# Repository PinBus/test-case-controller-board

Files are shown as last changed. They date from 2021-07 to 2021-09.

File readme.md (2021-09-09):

# Test-case Controller Board - Rev. 1.0

This board has been developed to control demo setups. It is essentially a smaller sized pinball machine controller. This board is based on the Arduino Uno, paired with a PCA9685 breakout board, eight MOSFETs and a four by four input matrix.

You will need to have a stencil made to make this board yourself. The SMD part footprints are not made for hand soldering.

**Warning: These designs are made as part of a hobby project and thus come with no guarantees. Do not use these designs in for any critical systems! Working with voltages higher than +40V can be potentially dangerous, please take appropriate safety measures!**

## Optional parts

 - Connectors **J2** and **J3** are optional. These headers expose the I2C bus and UART respectively.
 - Connectors **J4**, **J5**, and **J6** are optional. These headers expose the microcontroller pins.
 - Connector **J7** or **J8** are optional. These connectors are connected to the +5V rail. You will need at least one to power the board. The other connector can be used to power another board.
 - Connector **J9** or **J10** are optional. These connectors are connected to the +48V rail. You will need at least one when using the MOSFETs. The other connector can be used to power another board.
 - MOSFETs **Q1** thru **Q8** are optional:
   - Do not populate **R4**, **R6**, connector **SOL0**, and **D3** when not using **Q1**;
   - Do not populate **R8**, **R10**, connector **SOL1**, and **D4** when not using **Q2**;
   - Do not populate **R5**, **R7**, connector **SOL2**, and **D5** when not using **Q3**;
   - Do not populate **R9**, **R11**, connector **SOL3**, and **D6** when not using **Q4**;
   - Do not populate **R12**, **R14**, connector **SOL4**, and **D7** when not using **Q5**;
   - Do not populate **R16**, **R18**, connector **SOL5**, and **D8** when not using **Q6**;
   - Do not populate **R13**, **R15**, connector **SOL6**, and **D9** when not using **Q7**;
   - Do not populate **R17**, **R19**, connector **SOL7**, and **D10** when not using **Q8**;
 - When not using a MOSFET, you can use its pin on the PCA9685 to drive an LED:
   - Populate **LED0** if **Q1** is not used;
   - Populate **LED1** if **Q2** is not used;
   - Populate **LED2** if **Q3** is not used;
   - Populate **LED3** if **Q4** is not used;
   - Populate **LED4** if **Q5** is not used;
   - Populate **LED5** if **Q6** is not used;
   - Populate **LED6** if **Q7** is not used;
   - Populate **LED7** if **Q8** is not used;
 - **SOL0** and **SOL2** can be populated with either a 2 pin or a 3 pin connector:
   - Do not populate **SOL1** when **SOL0** is populated with a 3 pin connector;
   - Do not populate **SOL3** when **SOL2** is populated with a 3 pin connector;
 - All connectors and diodes making up the input matrix are optional:
   - Bridge **JP3** thru **JP6** to enable columns;
   - Bridge **JP7** thru **JP10** to enable rows;
 - Capacitors **C6** thru **C9** are optional. Populating **C6** is recommended. Populate others if needed.
 - Capacitors **C10** thru **C13** are optional. Populate if needed.

## BOM

| Identifiers | Quantity | Part number | Manufacturer | Footprint | Description |
| --- | ---: | --- | --- | --- | --- |
| C1 | 1x | CL10A475KQ8NNWC | Samsung Electro-Mechanics | 0603 | Capacitor, MLCC, 4.7μF, 10V |
| C2, C3, C4, C5 | 4x | GRM188R60J476ME15J  | Murata Electronics | 0603 | Capacitor, MLCC, 47μF, 6.3V |
| C6, C7, C8, C9 | 4x | URS1A470MDD1TA | Nichicon | ⌀5mm / 2mm  | Capacitor, Electrolytic, 47μ, 10V |
| C10, C11, C12, C13 | 4x | UVZ1J101MPD | Nichicon | ⌀10mm / 5mm | Capacitor, Electrolytic, 100μF, 63V |
| C14 | 1x | LMK107BBJ106MALT | Taiyo Yuden | 0603 | Capacitor, MLCC, 10μF, 10V |
| D1 | 1x | 150060RS75000 | Wurth Elektronik | 0603 | LED, Red |
| D2 | 1x | 150060GS75000 | Wurth Elektronik | 0603 | LED, Green |
| D3, D4, D5, D6, D7, D8, D9, D10 | 8x | S1M-13-F | Diodes Incorporated | SMA | Diode, rectifier, 1A, 1000V |
| D11, D12, D13, D14, D15, D16, D17, D18, D19, D20, D21, D22, D23, D24, D25, D26 | 16x | 1N4148W-G3-08 | Vishay / Dale | SOD-123 | Diode, general purpose, 150mA, 100V |
| J1 | 1x | | | 2.54mm | Connector, 2x3, Pin header |
| J2, J3 | 2x | B4B-XH-A(LF)(SN) | JST | 2.50mm | Connector, 1x4 |
| J4, J5 | 2x | | | 2.54mm | Connector, 1x8, pin header |
| J6 | 1x | | | 2.54mm | Connector, 1x6, pin header |
| J7, J8, LED0, LED1, LED2, LED3, LED4, LED5, LED6, LED7, LED8, LED9, LED10, LED11, LED12, LED13, LED14, LED15, MTX-0x0, MTX-0x1, MTX-0x2, MTX-0x3, MTX-1x0, MTX-1x1, MTX-1x2, MTX-1x3, MTX-2x0, MTX-2x1, MTX-2x2, MTX-2x3, MTX-3x0, MTX-3x1, MTX-3x2, MTX-3x3 | 34x | B2B-XH-A(LF)(SN) | JST | 2.50mm | Connector, 1x2 |
| J9, J10, SOL0, SOL1, SOL2, SOL3, SOL4, SOL5, SOL6, SOL7 | 10x | B2P-VH _or_ 1-1123723-3 | JST _or_ TE Connectivity | 3.96mm | Connector, 1x2 |
| JP1, JP2 | 2x | | | 2.54mm | Jumper wire |
| SOL0, SOL2 | 2x | B3P-VH _or_ 1-1123723-2 | JST _or_ TE Connectivity | 3.96mm | Connector, 1x3 |
| Q1, Q2, Q3, Q4, Q5, Q6, Q7, Q8 | 8x | IRL540NPBF | Infineon / IR | TO-220 | MOSFET, 100V, 36A |
| R1 | 1x | CRCW06034K70JNEAC | Vishay / Dale | 0603 | Resistor, 4.7kΩ |
| R2, R3 | 2x | CRCW06031K00FKEAC | Vishay / Dale | 0603 | Resistor, 1kΩ |
| R4, R5, R8, R9, R12, R13, R16, R17 | 8x | CRCW060310R0FKEAC | Vishay / Dale | 0603 | Resistor, 10Ω |
| R6, R7, R10, R11, R14, R15, R18, R19, R20, R21, R22, R23, R24, R25, R26, R27, R28, R29, R30, R31, R32 | 21x | CRCW060310K0JNEAC | Vishay / Dale | 0603 | Resistor, 10kΩ |
| SW1 | 1x | PTS810SJM250SMTRLFS | C&K | - | Switch |
| U1 | 1x | ATmega328P-AU | Microchip Technology | TQFP-32 | Microcontroller |
| U2 | 1x | PCA9685PW,112 | NXP Semiconductors | TSSOP-28 | PWM driver |
| Y1 | 1x | CSTNE16M0V53L00ZR0  | Murata Electronics | - | Resonator, 16MHz, 15pF |

### Pin headers

You can use either the [JST VH series](https://www.jst-mfg.com/product/detail_e.php?series=262) pin headers or the TE Connectivity Economy Power series pin headers. These pin headers are known to fit, other 3.96mm pin pitch pin headers might also fit.

 - Order the JST SVH-21T-P1.1 crimp contacts (0.34mm² - 0.75mm²) for use with the JST pin headers
 - Order JST VHR-2N connector housing for the JST B2P-VH pin header
 - Order JST VHR-3N connector housing for the JST B3P-VH pin header
 - Order the [TE Connectivity 1123721-2](https://www.te.com/usa-en/product-1123721-2.html) crimp contacts (0.34mm² - 0.75mm²) for use with the TE Connectivity pin headers
 - Order the [TE Connectivity 1-1123722-2](https://www.te.com/usa-en/product-1-1123722-2.html) connector housing for the [TE Connectivity 1-1123723-2](https://www.te.com/usa-en/product-1-1123723-2.html) pin header
 - Order the [TE Connectivity 1-1123722-3](https://www.te.com/usa-en/product-1-1123722-3.html) connector housing for the [TE Connectivity 1-1123723-3](https://www.te.com/usa-en/product-1-1123723-3.html) pin header

## Pictures

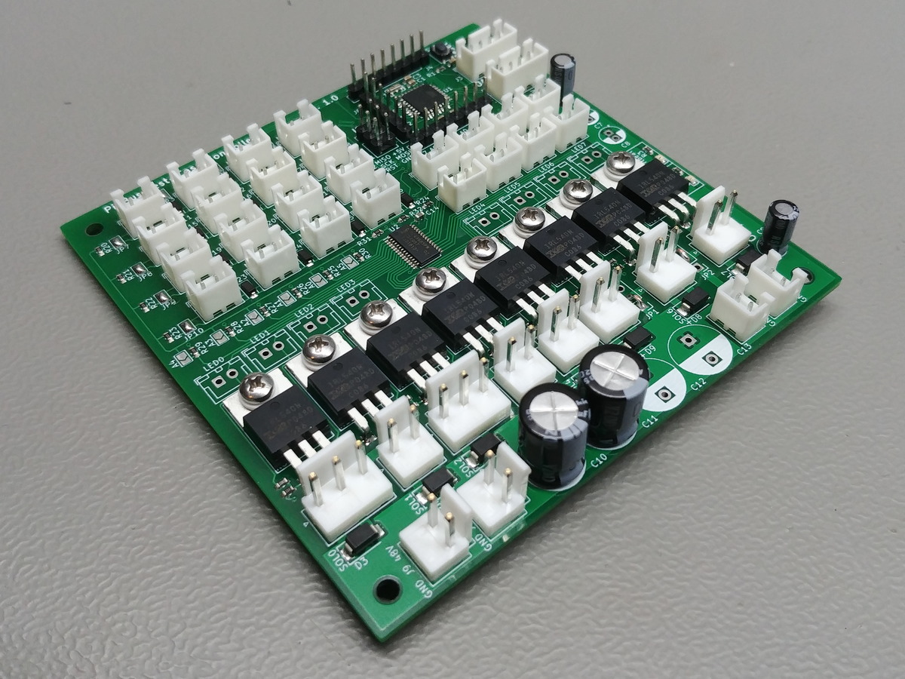
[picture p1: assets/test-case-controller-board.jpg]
Test-Case Controller Board


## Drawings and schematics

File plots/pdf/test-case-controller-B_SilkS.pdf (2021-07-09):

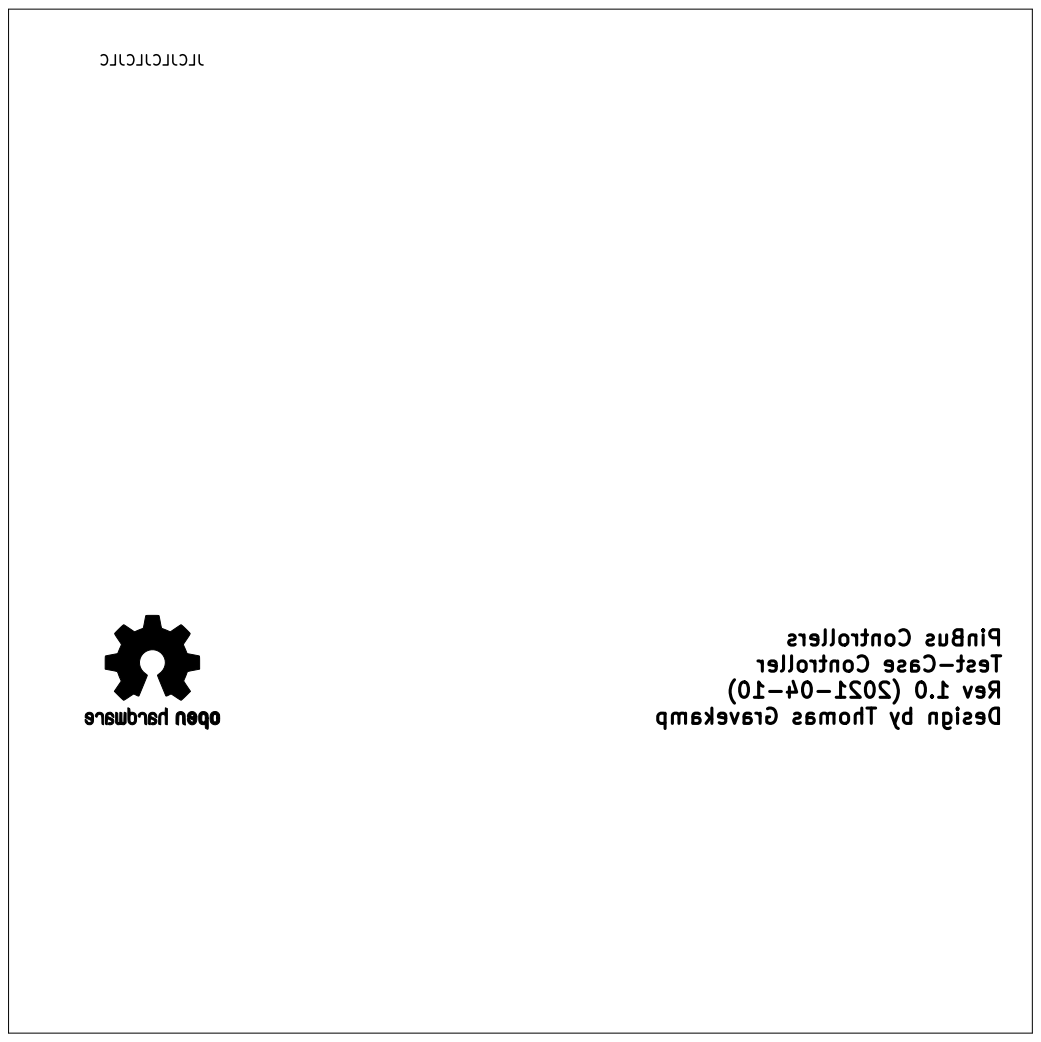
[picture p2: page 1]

JLCJLCJLCJLC PinBus Controllers Test-Case Controller Rev 1.0 (2021-04-10)

Design by Thomas Gravekamp

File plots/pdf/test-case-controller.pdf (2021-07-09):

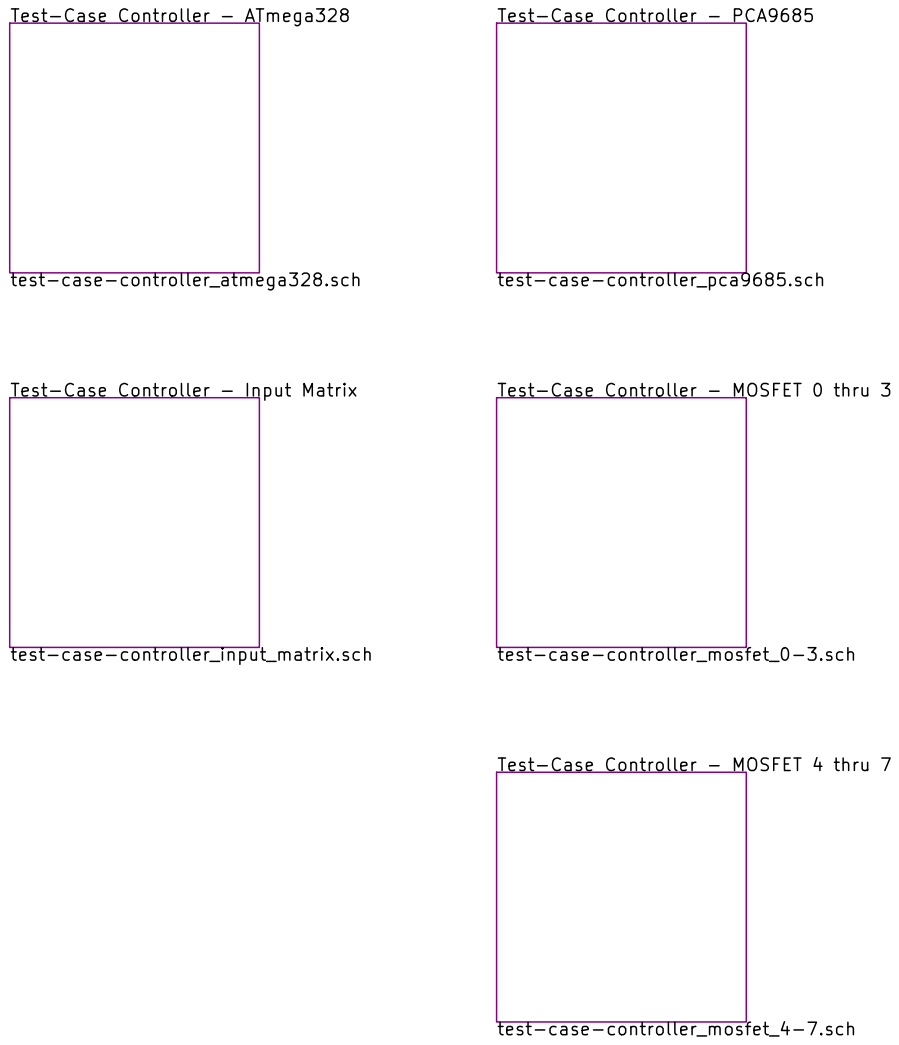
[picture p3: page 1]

test-case-controller_mosfet_4-7.sch Test-Case Controller - Input Matrix

test-case-controller_mosfet_0-3.sch Test-Case Controller - MOSFET 4 thru 7

File: test-case-controller.sch Sheet: / PinBus Design by Thomas Gravekamp Test-Case Controller

Id: 1/6 Title: Mainboard main schematic

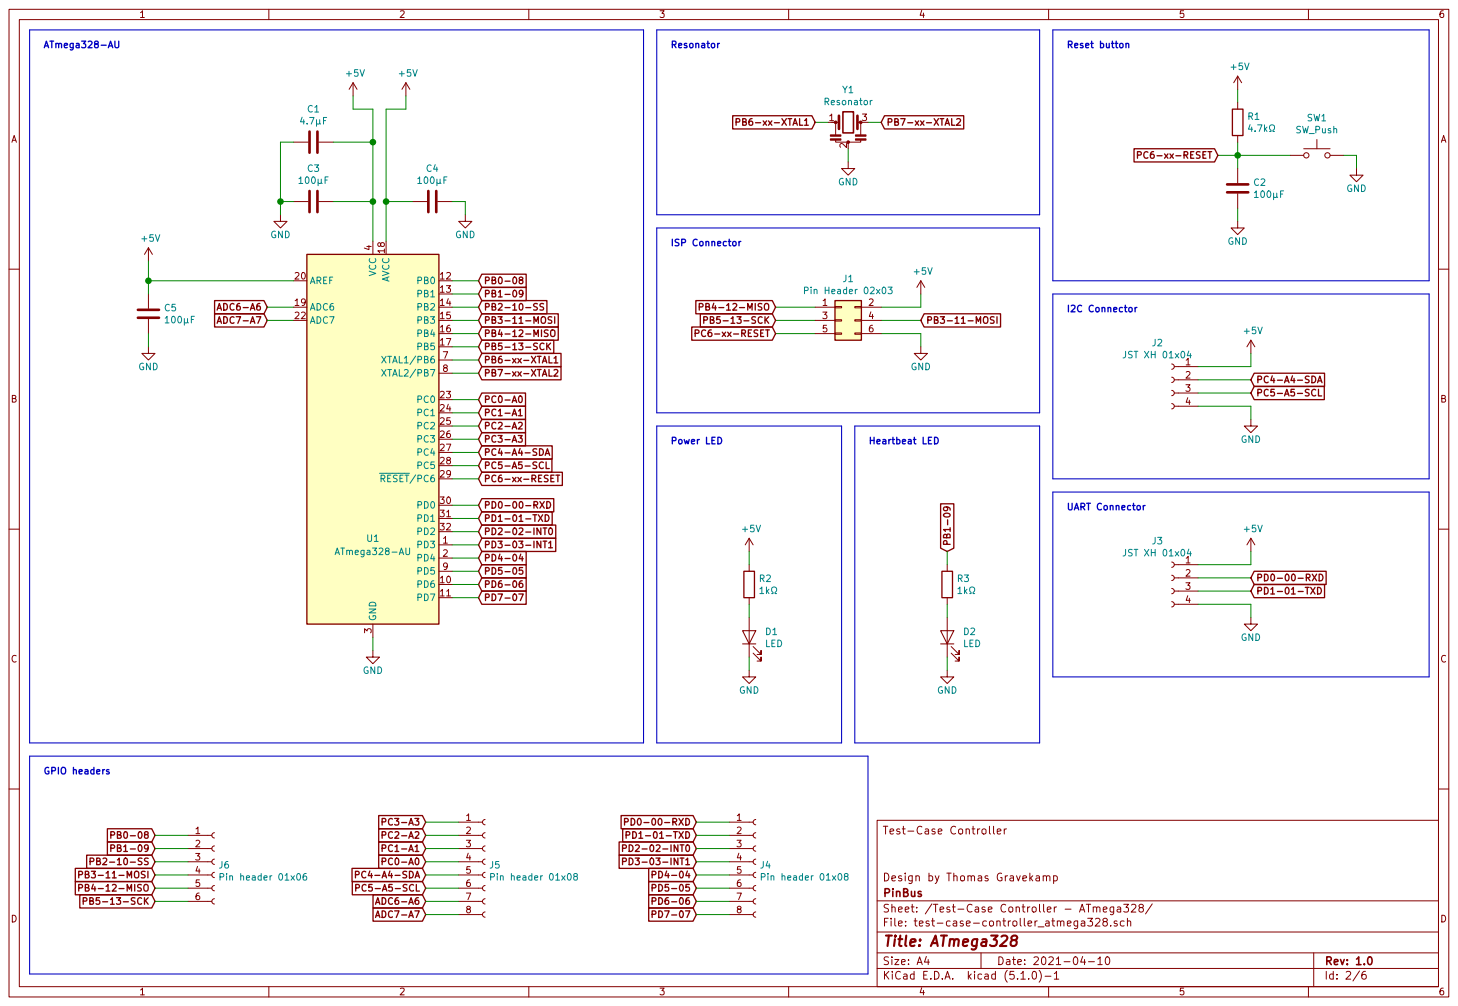
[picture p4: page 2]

4.7k PC6-xx-RESET PC6-xx-RESET PB5-13-SCK

PC5-A5-SCL PC6-xx-RESET PD0-00-RXD

Sheet: /Test-Case Controller - ATmega328/ PinBus Design by Thomas Gravekamp Test-Case Controller

File: test-case-controller_atmega328.sch
Id: 2/6 Title: ATmega328

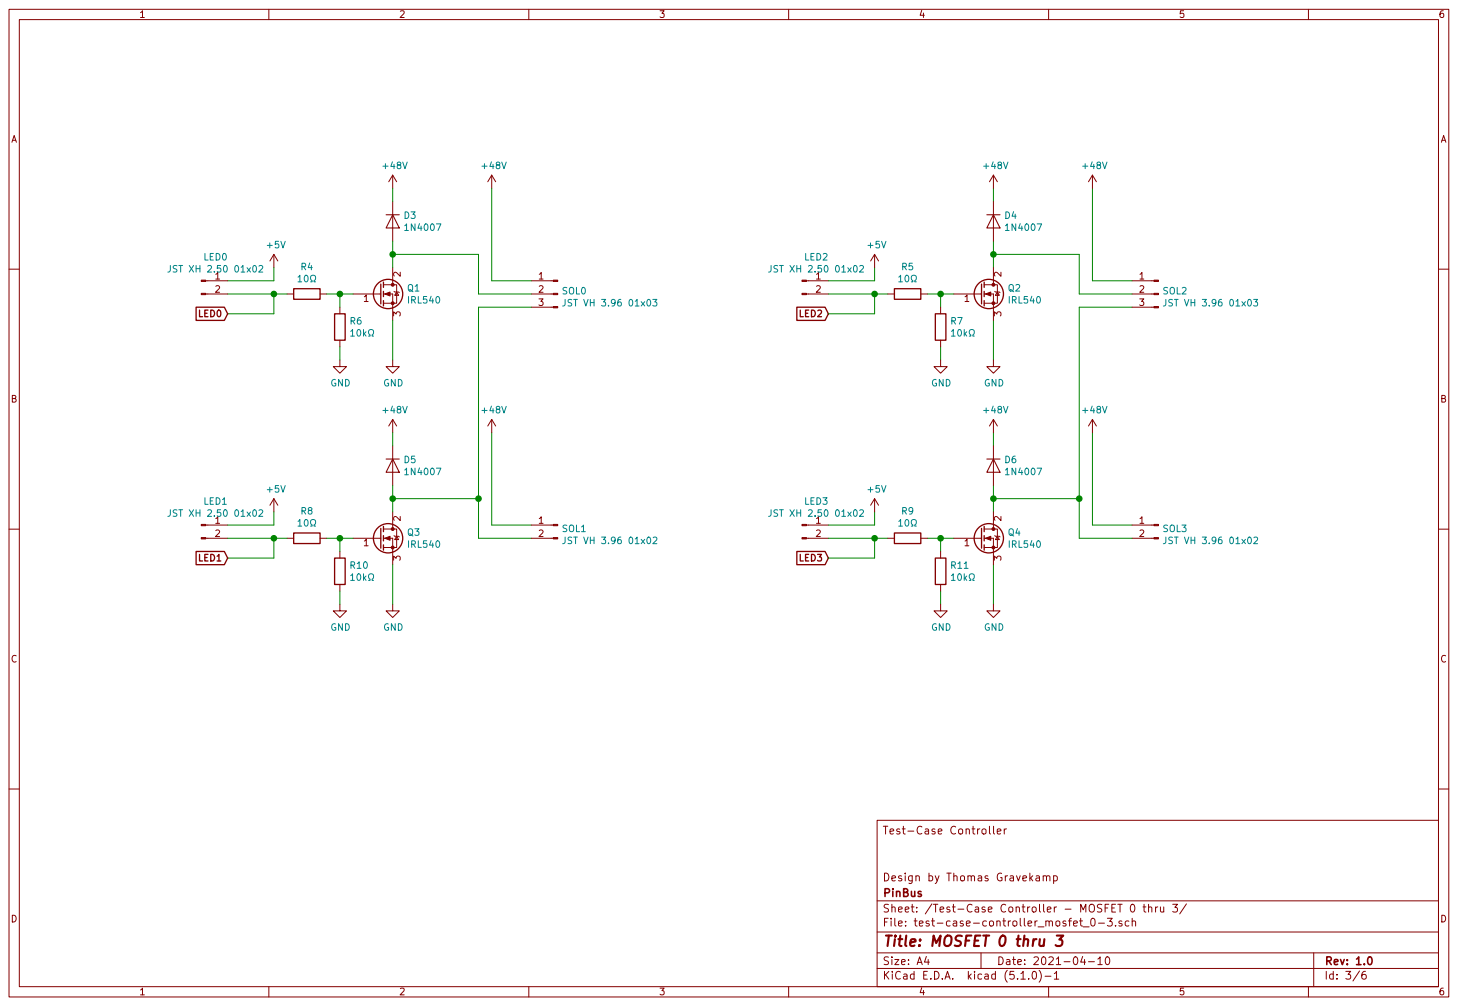
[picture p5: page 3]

File: test-case-controller_mosfet_0-3.sch Sheet: /Test-Case Controller - MOSFET 0 thru 3/ PinBus Design by Thomas Gravekamp Test-Case Controller

Id: 3/6 Title: MOSFET 0 thru 3

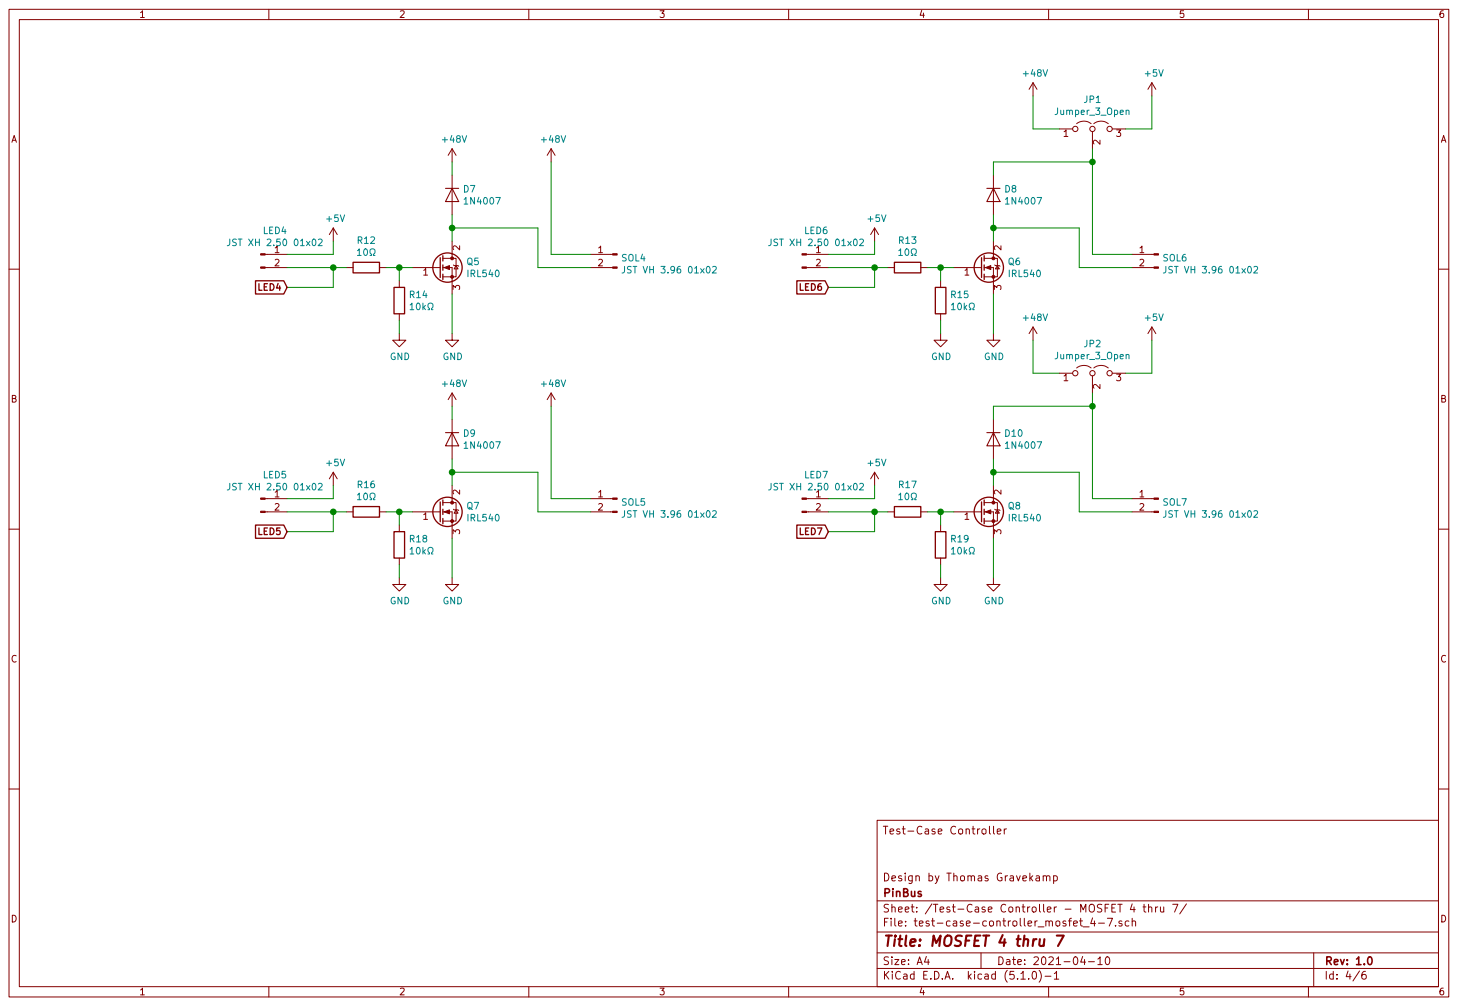
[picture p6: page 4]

File: test-case-controller_mosfet_4-7.sch Sheet: /Test-Case Controller - MOSFET 4 thru 7/ PinBus Design by Thomas Gravekamp Test-Case Controller

Id: 4/6 Title: MOSFET 4 thru 7

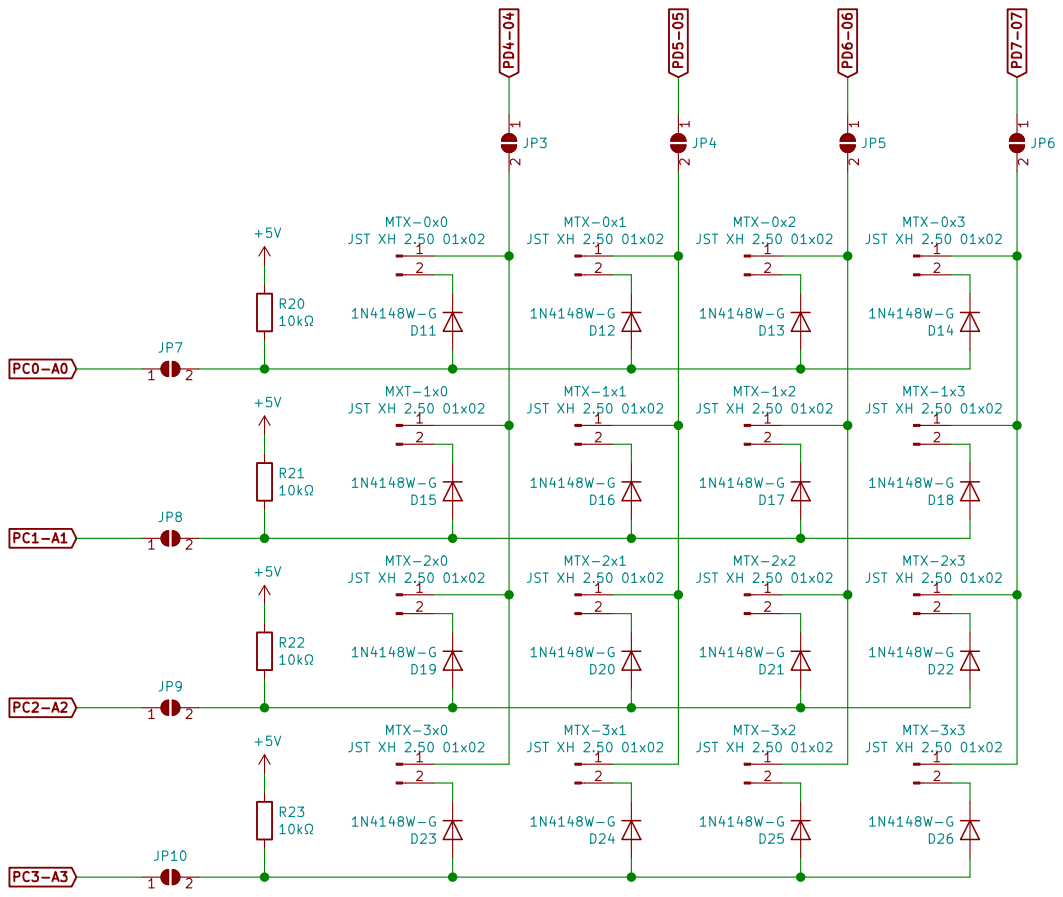
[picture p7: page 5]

File: test-case-controller_input_matrix.sch
Id: 5/6 Title: Input Matrix

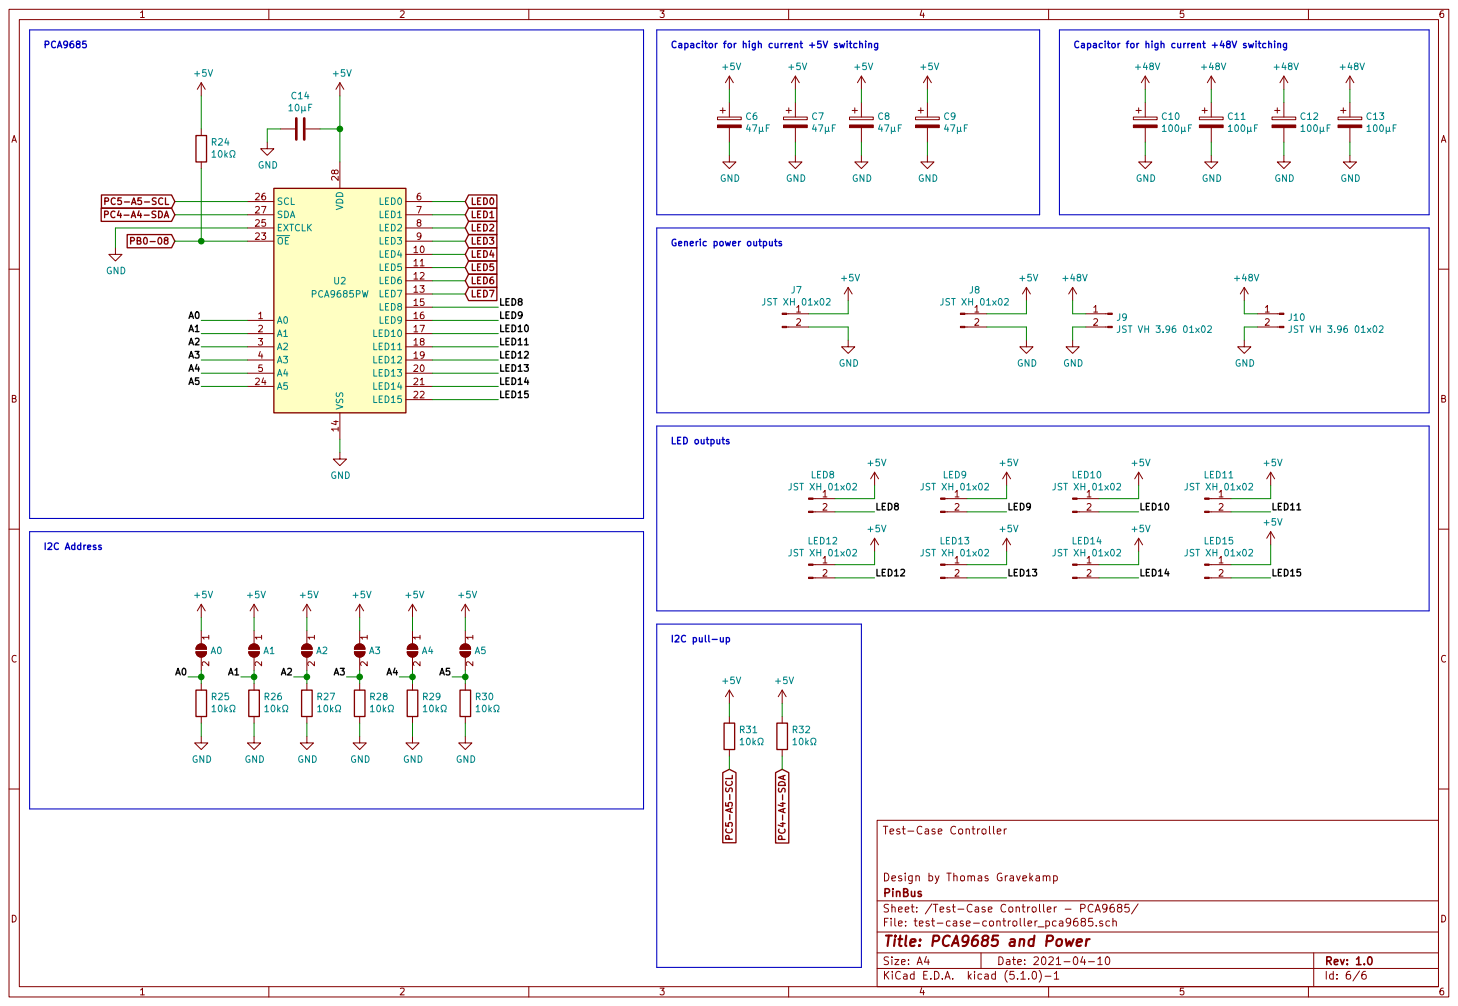
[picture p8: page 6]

+48V Capacitor for high current +48V switching

File: test-case-controller_pca9685.sch Sheet: /Test-Case Controller - PCA9685/ PinBus Design by Thomas Gravekamp Test-Case Controller

Id: 6/6 Title: PCA9685 and Power

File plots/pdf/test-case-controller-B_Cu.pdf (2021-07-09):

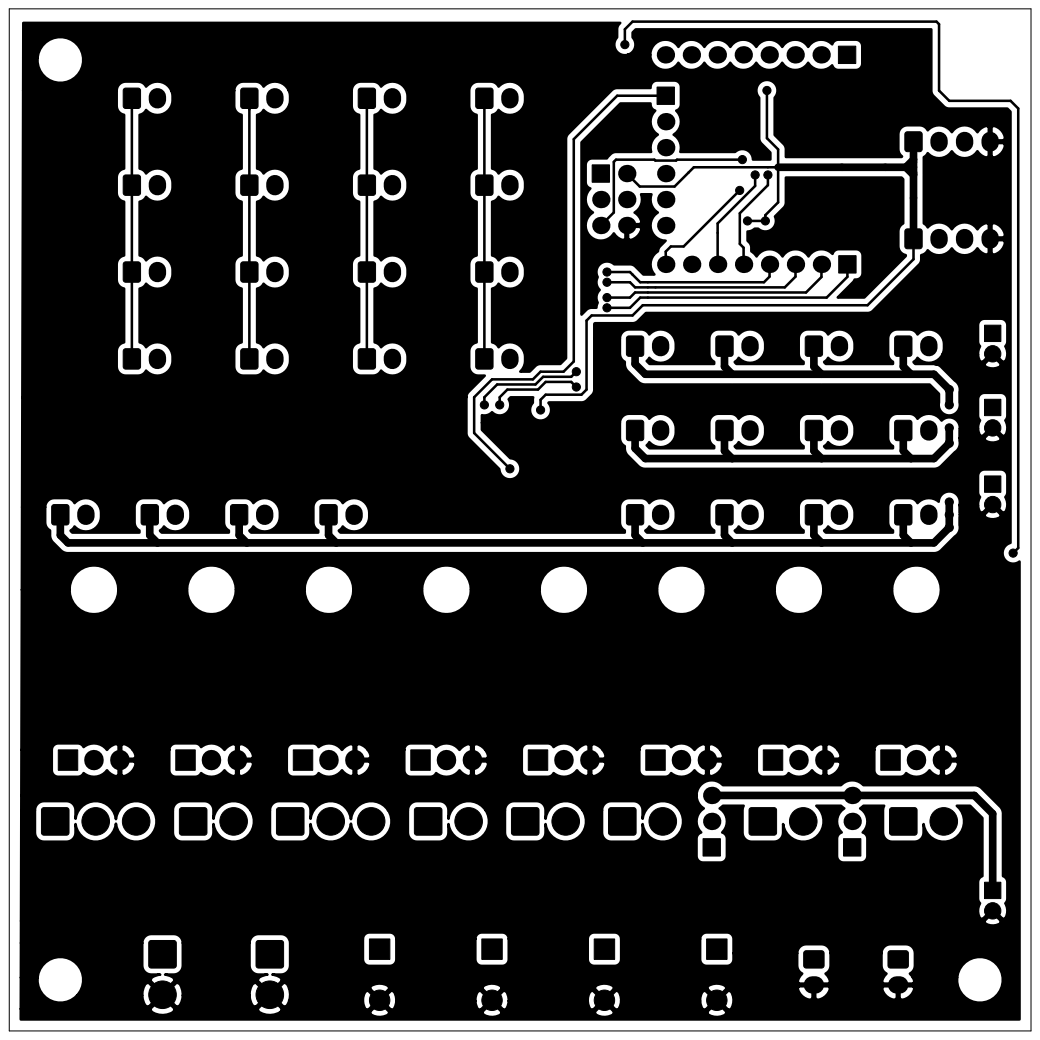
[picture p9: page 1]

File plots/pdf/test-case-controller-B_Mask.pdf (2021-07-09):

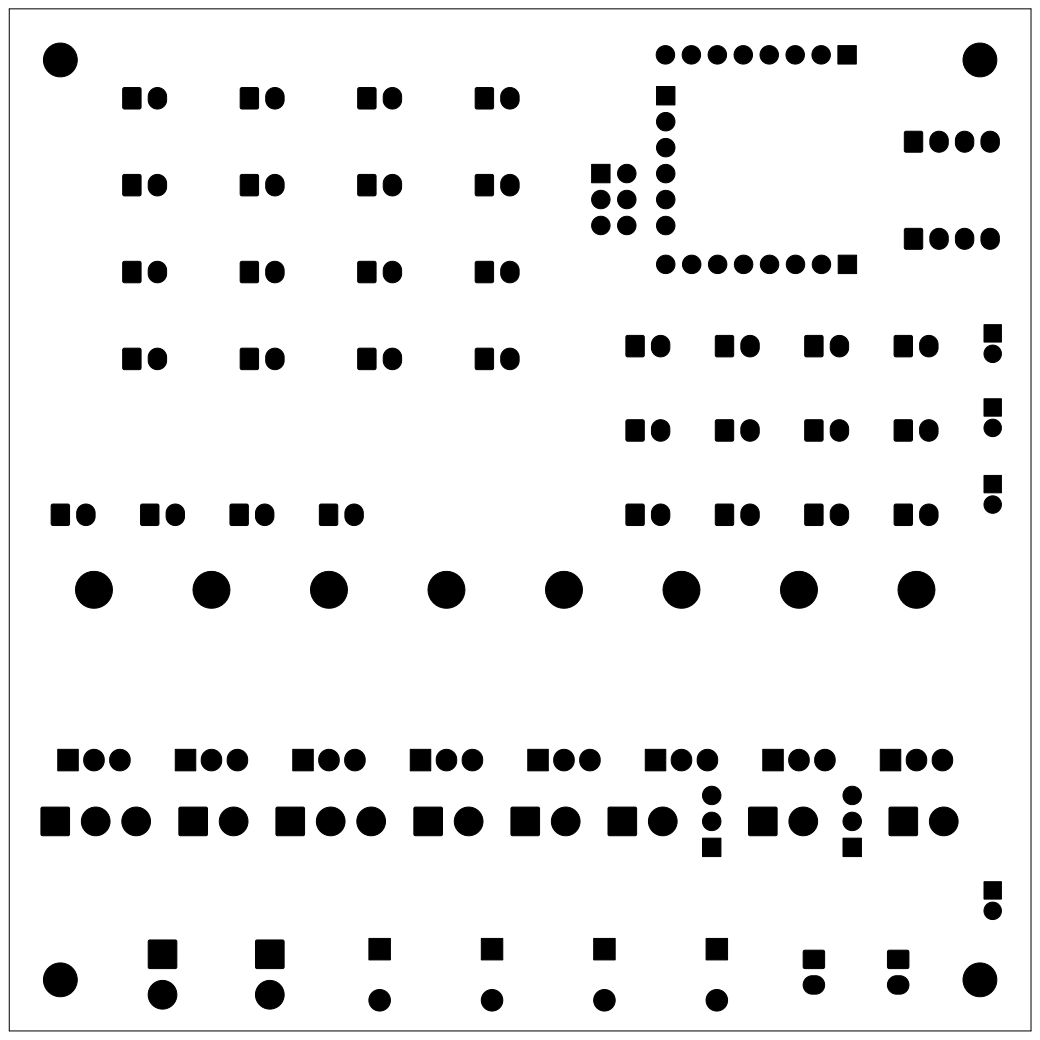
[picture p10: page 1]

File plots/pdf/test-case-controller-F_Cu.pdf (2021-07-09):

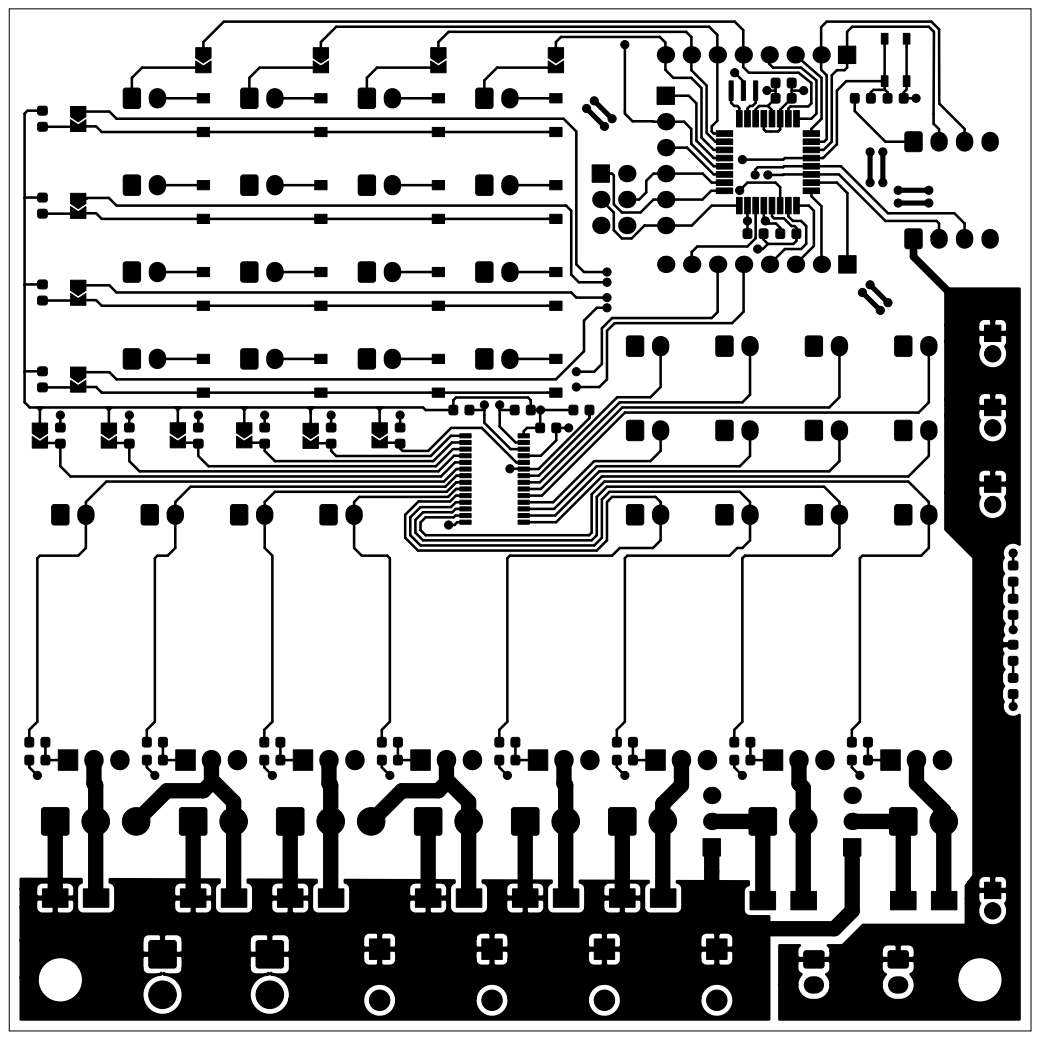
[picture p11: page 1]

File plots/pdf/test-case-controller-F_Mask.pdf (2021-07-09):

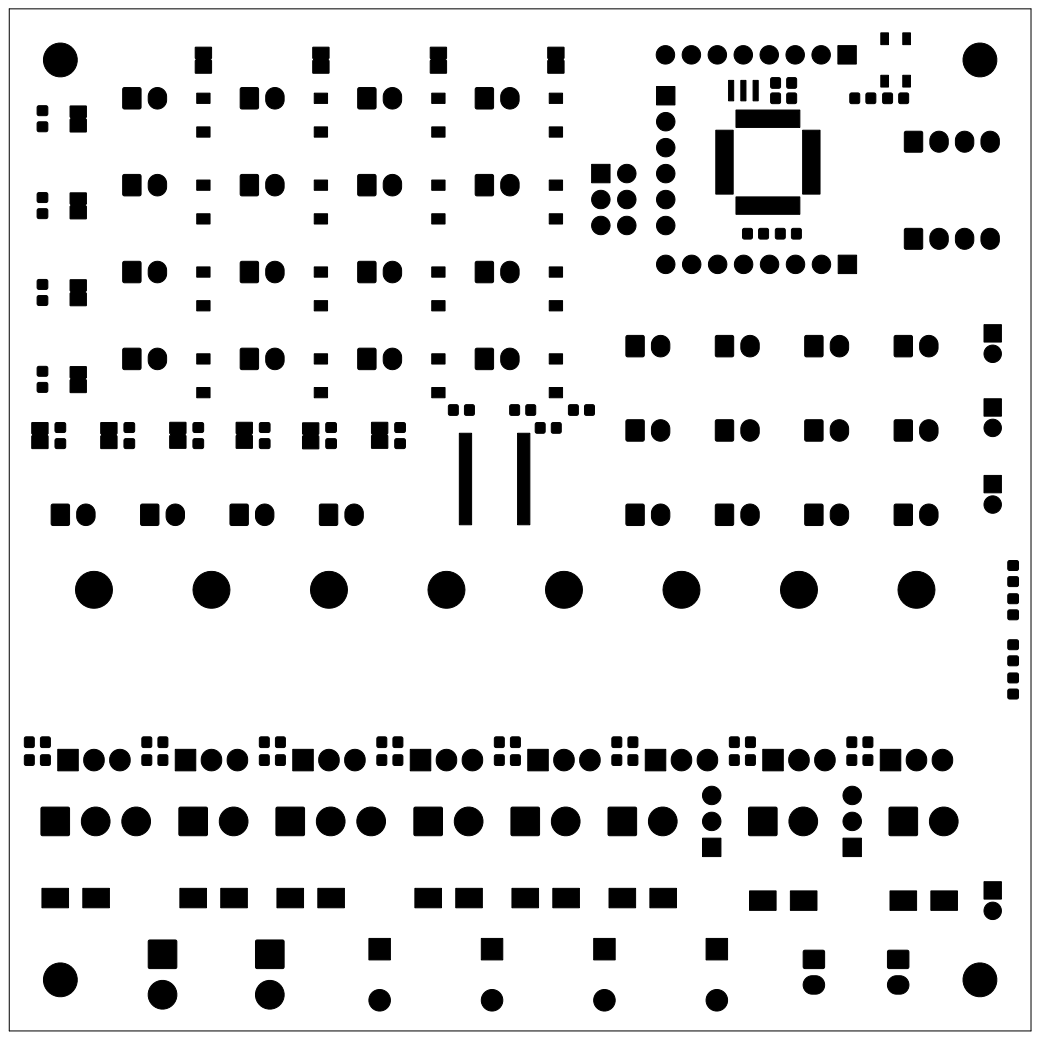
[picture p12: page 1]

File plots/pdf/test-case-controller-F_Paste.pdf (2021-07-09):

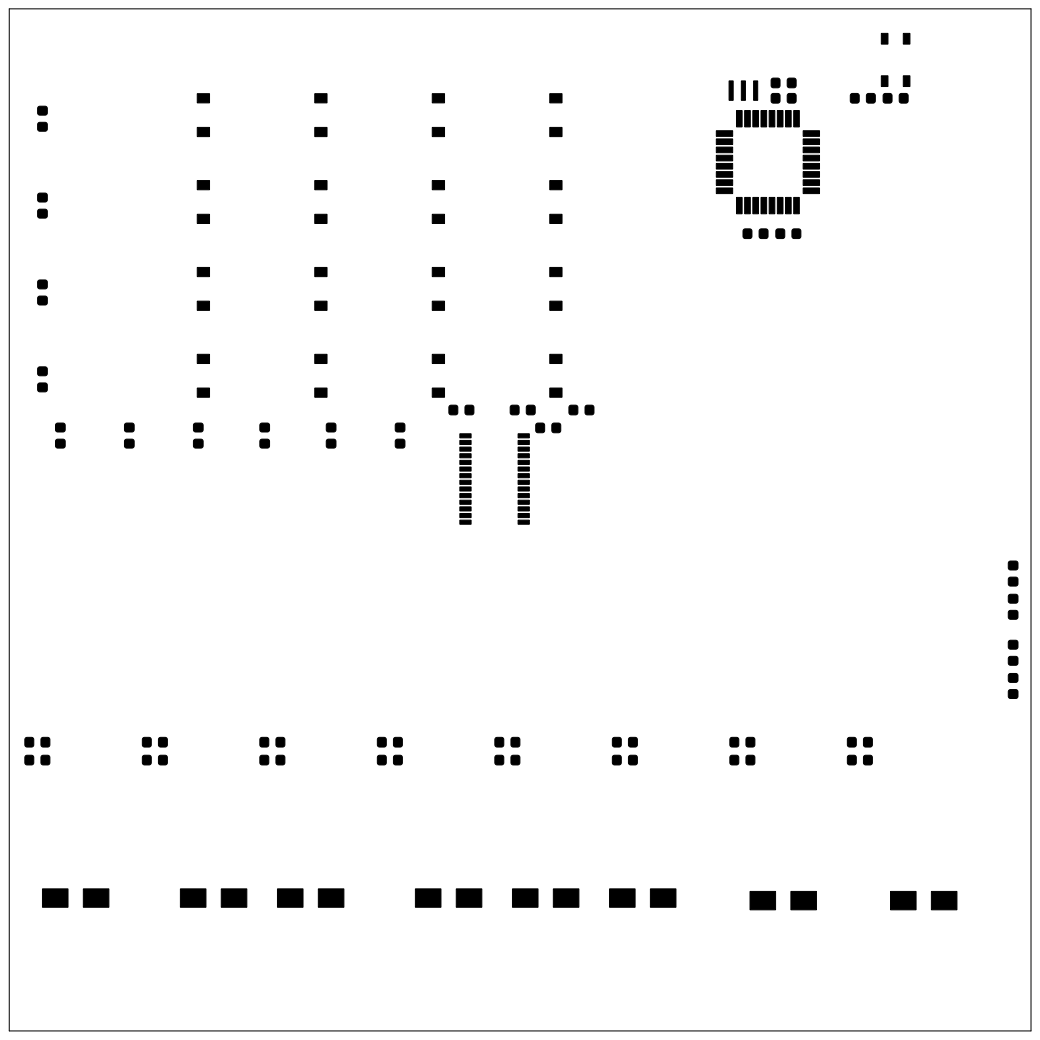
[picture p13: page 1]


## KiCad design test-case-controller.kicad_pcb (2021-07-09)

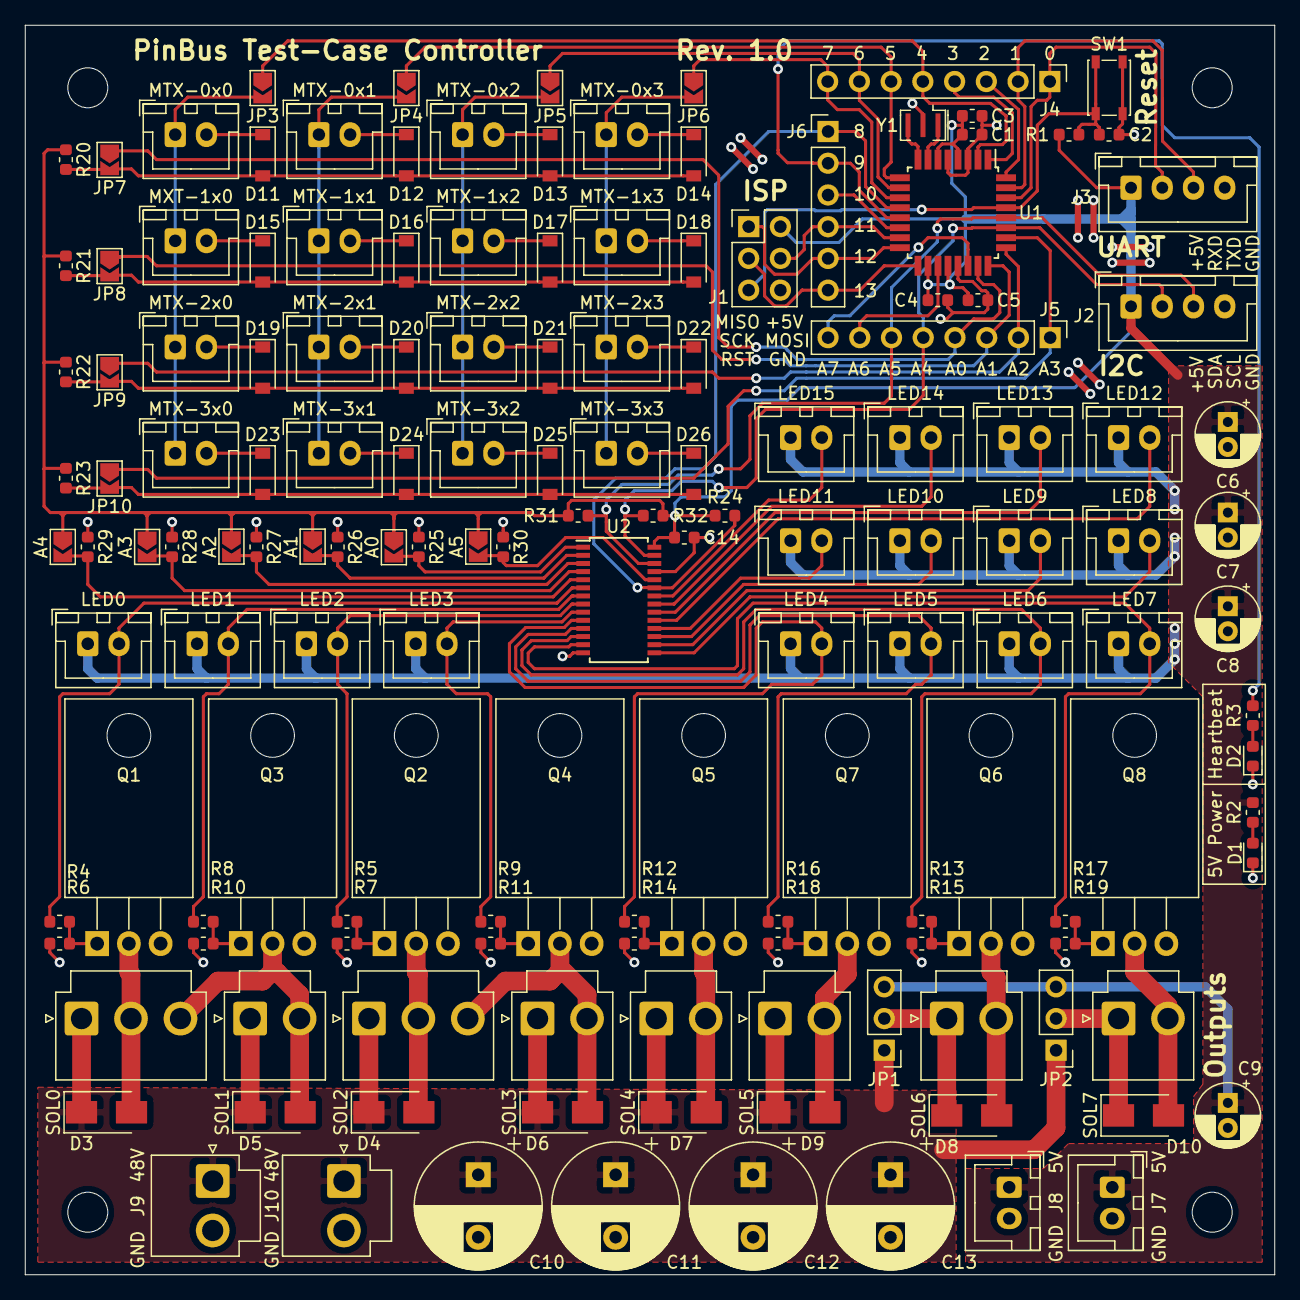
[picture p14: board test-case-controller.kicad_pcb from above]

Board: 2 copper layers, 100.0 x 100.0 mm, 150 parts (0 on the bottom side), 94 nets.

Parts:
A0, A1, A2, A3, A4, A5: SolderJumper_2_Open; SolderJumper-2_P1.3mm_Open_TrianglePad1.0x1.5mm
C1: 4.7μF; C_0603_1608Metric
C2, C3, C4, C5: 100μF; C_0603_1608Metric
C6, C7, C8, C9: 47μF; CP_Radial_D5.0mm_P2.00mm
C10, C11, C12, C13: 100μF; CP_Radial_D10.0mm_P5.00mm
C14: 10μF; C_0603_1608Metric
D1, D2: LED; LED_0603_1608Metric
D3, D4, D5, D6, D7, D8, D9, D10: 1N4007; D_SMA
D11, D12, D13, D14, D15, D16, D17, D18, D19, D20, D21, D22, D23, D24, D25, D26: 1N4148W-G; D_SOD-123
J1: Pin Header 02x03; PinHeader_2x03_P2.54mm_Vertical
J2, J3: JST XH 01x04; JST_XH_B4B-XH-A_1x04_P2.50mm_Vertical
J4, J5: Pin header 01x08; PinHeader_1x08_P2.54mm_Vertical
J6: Pin header 01x06; PinHeader_1x06_P2.54mm_Vertical
J7, J8: JST XH 01x02; JST_XH_B2B-XH-A_1x02_P2.50mm_Vertical
J9, J10: JST VH 3.96 01x02; JST_VH_B2P-VH_1x02_P3.96mm_Vertical
JP1, JP2: Jumper_3_Open; PinHeader_1x03_P2.54mm_Vertical
JP3, JP4, JP5, JP6, JP7, JP8, JP9, JP10: SolderJumper_2_Open; SolderJumper-2_P1.3mm_Open_TrianglePad1.0x1.5mm
LED0, LED1, LED2, LED3, LED4, LED5, LED6, LED7: JST XH 2.50 01x02; JST_XH_B2B-XH-A_1x02_P2.50mm_Vertical
LED8, LED9, LED10, LED11, LED12, LED13, LED14, LED15: JST XH 01x02; JST_XH_B2B-XH-A_1x02_P2.50mm_Vertical
MTX-0x0, MTX-0x1, MTX-0x2, MTX-0x3, MTX-1x1, MTX-1x2, MTX-1x3, MTX-2x0, MTX-2x1, MTX-2x2, MTX-2x3, MTX-3x0, MTX-3x1, MTX-3x2, MTX-3x3: JST XH 2.50 01x02; JST_XH_B2B-XH-A_1x02_P2.50mm_Vertical
MXT-1x0: JST XH 2.50 01x02; JST_XH_B2B-XH-A_1x02_P2.50mm_Vertical
Q1, Q2, Q3, Q4, Q5, Q6, Q7, Q8: IRL540; TO-220-3_Horizontal_TabDown
R1: 4.7kΩ; R_0603_1608Metric
R2, R3: 1kΩ; R_0603_1608Metric
R4, R5, R8, R9, R12, R13, R16, R17: 10Ω; R_0603_1608Metric
R6, R7, R10, R11, R14, R15, R18, R19, R20, R21, R22, R23, R24, R25, R26, R27, R28, R29, R30, R31, R32: 10kΩ; R_0603_1608Metric
SOL0, SOL2: JST VH 3.96 01x03; JST_VH_B3P-VH_1x03_P3.96mm_Vertical
SOL1, SOL3, SOL4, SOL5, SOL6, SOL7: JST VH 3.96 01x02; JST_VH_B2P-VH_1x02_P3.96mm_Vertical
SW1: SW_Push; SW_SPST_PTS810
U1: ATmega328-AU; TQFP-32_7x7mm_P0.8mm
U2: PCA9685PW; TSSOP-28_4.4x9.7mm_P0.65mm
Y1: Resonator; Resonator_SMD_muRata_CSTxExxV-3Pin_3.0x1.1mm

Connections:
+5V: A0.1, A1.1, A2.1, A3.1, A4.1, A5.1, C1.1, C3.1, C4.2, C5.1, C6.1, C7.1, C8.1, C9.1, C14.1, J1.2, J2.1, J3.1, J7.1, J8.1, JP1.3, JP2.3, LED0.1, LED1.1, LED2.1, LED3.1, LED4.1, LED5.1, LED6.1, LED7.1, LED8.1, LED9.1, LED10.1, LED11.1, LED12.1, LED13.1, LED14.1, LED15.1, R1.1, R2.1, R20.1, R21.1, R22.1, R23.1, R24.2, R31.2, R32.2, U1.4, U1.6, U1.18, U1.20, U2.28
+48V: C10.1, C11.1, C12.1, C13.1, D3.1, D4.1, D5.1, D6.1, D7.1, D9.1, J9.1, J10.1, JP1.1, JP2.1, SOL0.1, SOL1.1, SOL2.1, SOL3.1, SOL4.1, SOL5.1
/Mainboard PCA9685/A0: A0.2, R25.2, U2.1
/Mainboard PCA9685/A1: A1.2, R26.2, U2.2
/Mainboard PCA9685/A2: A2.2, R27.2, U2.3
/Mainboard PCA9685/A3: A3.2, R28.2, U2.4
/Mainboard PCA9685/A4: A4.2, R29.2, U2.5
/Mainboard PCA9685/A5: A5.2, R30.2, U2.24
/Mainboard PCA9685/LED8: LED8.2, U2.15
/Mainboard PCA9685/LED9: LED9.2, U2.16
/Mainboard PCA9685/LED10: LED10.2, U2.17
/Mainboard PCA9685/LED11: LED11.2, U2.18
/Mainboard PCA9685/LED12: LED12.2, U2.19
/Mainboard PCA9685/LED13: LED13.2, U2.20
/Mainboard PCA9685/LED14: LED14.2, U2.21
/Mainboard PCA9685/LED15: LED15.2, U2.22
ADC6-A6: J5.7, U1.19
ADC7-A7: J5.8, U1.22
GND: C1.2, C2.2, C3.2, C4.1, C5.2, C6.2, C7.2, C8.2, C9.2, C10.2, C11.2, C12.2, C13.2, C14.2, D1.1, D2.1, J1.6, J2.4, J3.4, J7.2, J8.2, J9.2, J10.2, Q1.3, Q2.3, Q3.3, Q4.3, Q5.3, Q6.3, Q7.3, Q8.3, R6.2, R7.2, R10.2, R11.2, R14.2, R15.2, R18.2, R19.2, R25.1, R26.1, R27.1, R28.1, R29.1, R30.1, SW1.2, U1.3, U1.5, U1.21, U2.14, U2.25, Y1.2
LED0: LED0.2, R4.2, U2.6
LED1: LED1.2, R8.2, U2.7
LED2: LED2.2, R5.2, U2.8
LED3: LED3.2, R9.2, U2.9
LED4: LED4.2, R12.2, U2.10
LED5: LED5.2, R16.2, U2.11
LED6: LED6.2, R13.2, U2.12
LED7: LED7.2, R17.2, U2.13
unnamed: D1.2, R2.2
unnamed: D2.2, R3.2
unnamed: D3.2, Q1.2, SOL0.2
unnamed: D4.2, Q2.2, SOL2.2
unnamed: D5.2, Q3.2, SOL0.3, SOL1.2
unnamed: D6.2, Q4.2, SOL2.3, SOL3.2
unnamed: D7.2, Q5.2, SOL4.2
unnamed: D8.1, JP1.2, SOL6.1
unnamed: D8.2, Q6.2, SOL6.2
unnamed: D9.2, Q7.2, SOL5.2
unnamed: D10.1, JP2.2, SOL7.1
unnamed: D10.2, Q8.2, SOL7.2
unnamed: D11.1, MTX-0x0.2
unnamed: D11.2, D12.2, D13.2, D14.2, JP7.2, R20.2
unnamed: D12.1, MTX-0x1.2
unnamed: D13.1, MTX-0x2.2
unnamed: D14.1, MTX-0x3.2
unnamed: D15.1, MXT-1x0.2
unnamed: D15.2, D16.2, D17.2, D18.2, JP8.2, R21.2
unnamed: D16.1, MTX-1x1.2
unnamed: D17.1, MTX-1x2.2
unnamed: D18.1, MTX-1x3.2
unnamed: D19.1, MTX-2x0.2
unnamed: D19.2, D20.2, D21.2, D22.2, JP9.2, R22.2
unnamed: D20.1, MTX-2x1.2
unnamed: D21.1, MTX-2x2.2
unnamed: D22.1, MTX-2x3.2
unnamed: D23.1, MTX-3x0.2
unnamed: D23.2, D24.2, D25.2, D26.2, JP10.2, R23.2
unnamed: D24.1, MTX-3x1.2
unnamed: D25.1, MTX-3x2.2
unnamed: D26.1, MTX-3x3.2
unnamed: JP3.2, MTX-0x0.1, MTX-2x0.1, MTX-3x0.1, MXT-1x0.1
unnamed: JP4.2, MTX-0x1.1, MTX-1x1.1, MTX-2x1.1, MTX-3x1.1
unnamed: JP5.2, MTX-0x2.1, MTX-1x2.1, MTX-2x2.1, MTX-3x2.1
unnamed: JP6.2, MTX-0x3.1, MTX-1x3.1, MTX-2x3.1, MTX-3x3.1
unnamed: Q1.1, R4.1, R6.1
unnamed: Q2.1, R5.1, R7.1
unnamed: Q3.1, R8.1, R10.1
unnamed: Q4.1, R9.1, R11.1
unnamed: Q5.1, R12.1, R14.1
unnamed: Q6.1, R13.1, R15.1
unnamed: Q7.1, R16.1, R18.1
unnamed: Q8.1, R17.1, R19.1
PB0-08: J6.1, R24.1, U1.12, U2.23
PB1-09: J6.2, R3.1, U1.13
PB2-10-SS: J6.3, U1.14
PB3-11-MOSI: J1.4, J6.4, U1.15
PB4-12-MISO: J1.1, J6.5, U1.16
PB5-13-SCK: J1.3, J6.6, U1.17
PB6-xx-XTAL1: U1.7, Y1.1
PB7-xx-XTAL2: U1.8, Y1.3
PC0-A0: J5.4, JP7.1, U1.23
PC1-A1: J5.3, JP8.1, U1.24
PC2-A2: J5.2, JP9.1, U1.25
PC3-A3: J5.1, JP10.1, U1.26
PC4-A4-SDA: J2.2, J5.5, R32.1, U1.27, U2.27
PC5-A5-SCL: J2.3, J5.6, R31.1, U1.28, U2.26
PC6-xx-RESET: C2.1, J1.5, R1.2, SW1.1, U1.29
PD0-00-RXD: J3.2, J4.1, U1.30
PD1-01-TXD: J3.3, J4.2, U1.31
PD2-02-INT0: J4.3, U1.32
PD3-03-INT1: J4.4, U1.1
PD4-04: J4.5, JP3.1, U1.2
PD5-05: J4.6, JP4.1, U1.9
PD6-06: J4.7, JP5.1, U1.10
PD7-07: J4.8, JP6.1, U1.11

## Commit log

2021-07-09 Add board files
    [test-case-controller-B_Cu.gbr, test-case-controller-B_Mask.gbr, test-case-controller-B_SilkS.gbr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]
2021-09-09 Add more information on power connectors and their alternatives
